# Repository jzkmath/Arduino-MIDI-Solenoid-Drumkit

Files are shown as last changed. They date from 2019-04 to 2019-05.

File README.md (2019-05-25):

# Arduino-MIDI-Solenoid-Drumkit
Uses an Arduino Mega and a custom Shield PCB to drive 14 solenoids (RevA) or 32 solenoids (RevB) via MIDI

## Rev A:
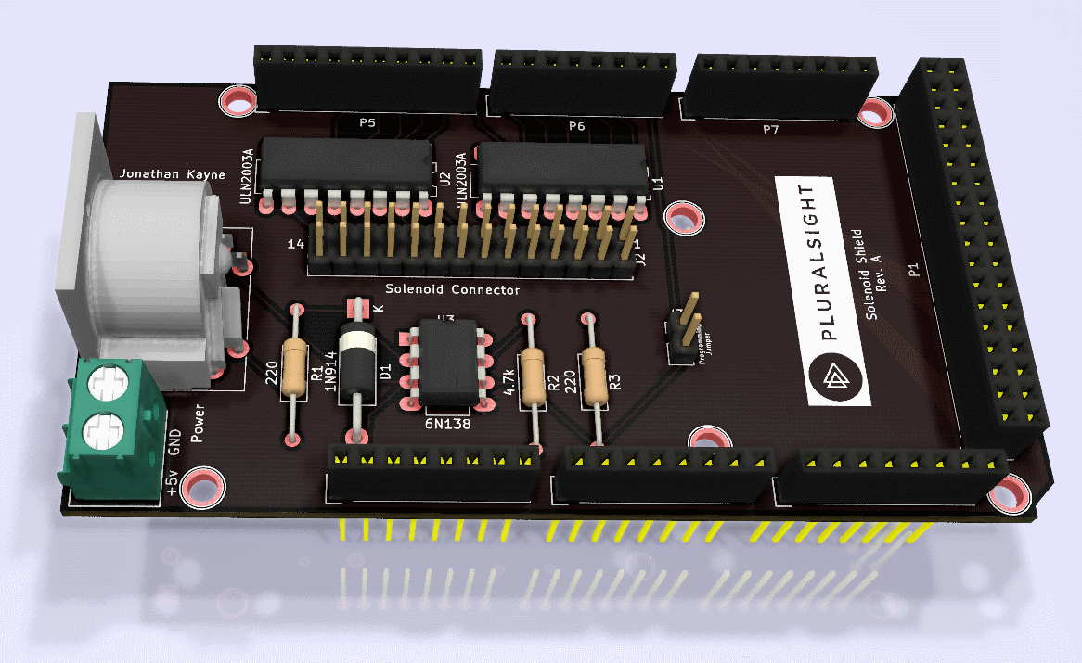
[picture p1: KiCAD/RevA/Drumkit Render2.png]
PCB RevA

## Rev B:
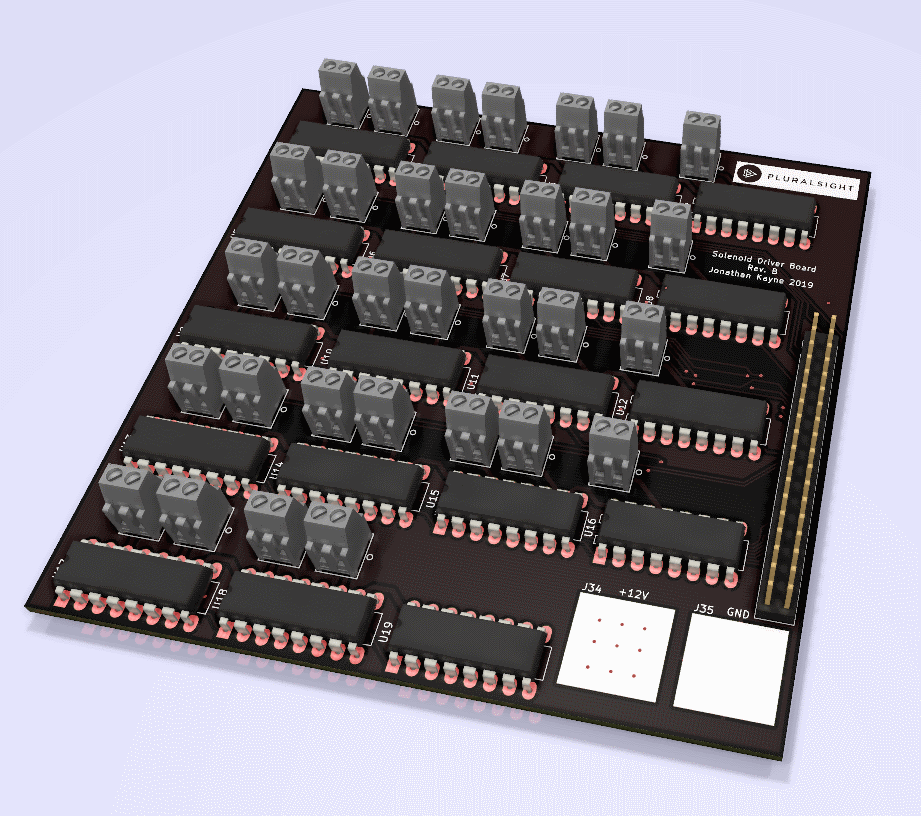
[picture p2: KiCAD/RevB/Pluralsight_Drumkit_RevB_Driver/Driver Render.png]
PCB RevB


This design is based off the [Adafruit Crikit](https://www.adafruit.com/product/3343) and MIDI Solenoid Drumkit that they did, but instead uses a non-blocking delay and can handle more solenoids. The Solenoids are connected to 5V/12V and a Darlington Array (ULN2003A) connects the negative to ground when turned on. 

Just like in the [Adafuit version](https://learn.adafruit.com/midi-solenoid-drummer/overview), the first solenoid corresponds to a C1 (MIDI Note #24) and the following solenoids correspond to the following notes in chromatic order.

## NOTE:
There is a two pin header (J3) that is the programming jumper. The jumper should be installed here and removed when the Arduino is being programmed. This is because the MIDI Rx line is also use to program the Arduino when its being flashed.

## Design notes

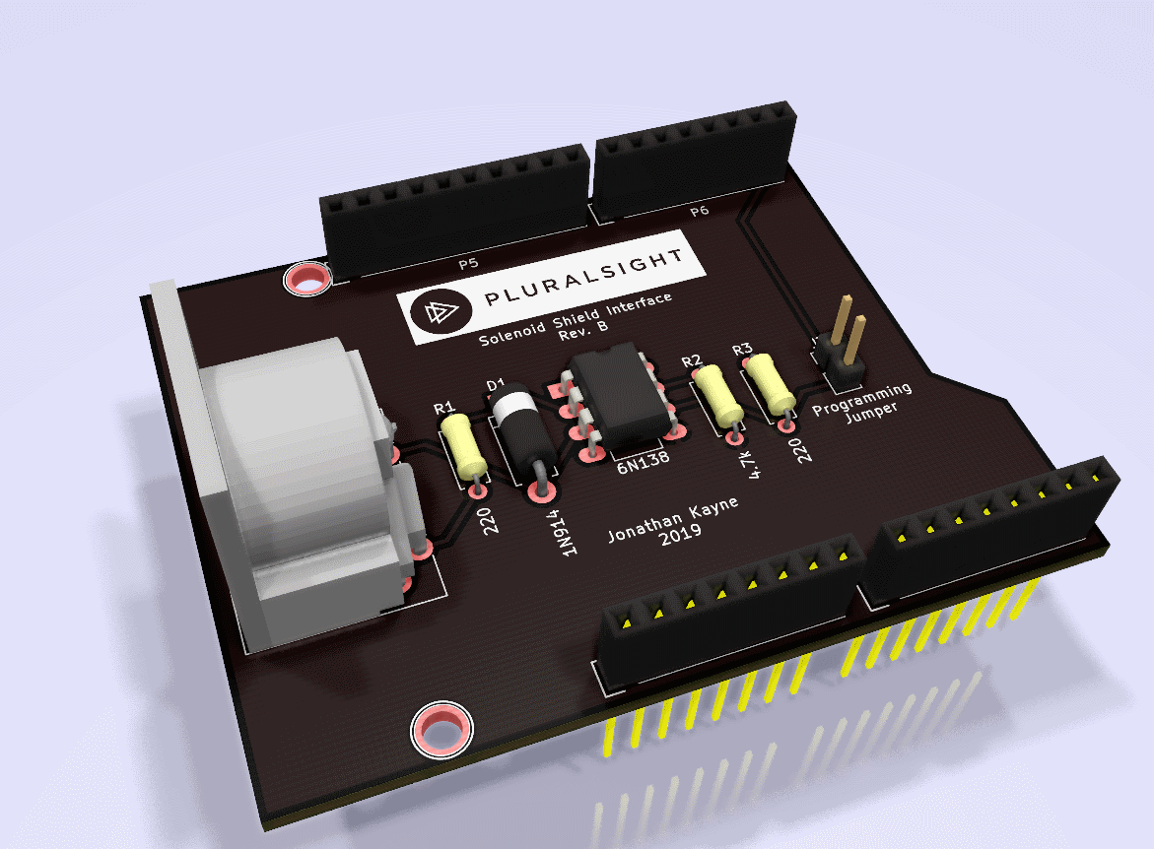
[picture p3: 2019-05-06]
KiCAD/RevB/Pluralsight_Drumkit_RevB_Interface/Interface Render.png

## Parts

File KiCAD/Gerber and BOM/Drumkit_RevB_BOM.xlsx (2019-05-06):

Board | Qty | Reference(s) | Value | Digikey | Cost | Total | Link | Total: | $43.96
Driver | 32 | J1-J33 | 2 pos Screw Terminal | A98333-ND | $0.58 | $18.51 | https://www.digikey.com/short/pzbmff
Both | 2 | J25, P1 | 2x18 Header | 732-5309-ND | $1.72 | $3.44 | https://www.digikey.com/short/pzbh4n
Driver | 2 | J34, J35 | Power | N/A | $0.00 | $0.00 | N/A
Driver | 19 | U1-U19 | ULN2003A | 497-2344-5-ND | $0.59 | $11.21 | https://www.digikey.com/short/pzbmvp
Driver | 19 | U1-U19 | DIP16 Socket | AE9992-ND | $0.24 | $4.48 | https://www.digikey.com/short/pzbm03
Interface | 1 | D1 | 1N914 | 1N914FS-ND | $0.10 | $0.10 | https://www.digikey.com/short/pzbhm2
Interface | 1 | J1 | MIDI DIN Connector | CP-2350-ND | $1.96 | $1.96 | https://www.digikey.com/short/pzbhhp
Interface | 1 | J3 | 1x2 Header | 732-5315-ND | $0.13 | $0.13 | https://www.digikey.com/short/pzbhhw
Interface | 5 | P2-P7 | 1x8 Header | 732-5321-ND | $0.37 | $1.85 | https://www.digikey.com/short/pzbh9m
Interface | 1 | P5 | 1x10 Header | 732-2670-ND | $0.89 | $0.89 | https://www.digikey.com/short/pzbh9v
Interface | 2 | R1, R3 | 220 ohm | S220QCT-ND | $0.10 | $0.20 | https://www.digikey.com/short/pzbhb3
Interface | 1 | R2 | 4.7k | S4.7KQCT-ND | $0.10 | $0.10 | https://www.digikey.com/short/pzbhbw
Interface | 1 | U3 | 6N138 | 160-1795-ND | $0.81 | $0.81 | https://www.digikey.com/short/pzbhrn
Interface | 1 | U3 | DIP8 Socket | AE9986-ND | $0.18 | $0.18 | https://www.digikey.com/short/pzbhft
Interface | 1 | J3 | Jumper | S9337-ND | $0.10 | $0.10 | https://www.digikey.com/short/pzbhf5

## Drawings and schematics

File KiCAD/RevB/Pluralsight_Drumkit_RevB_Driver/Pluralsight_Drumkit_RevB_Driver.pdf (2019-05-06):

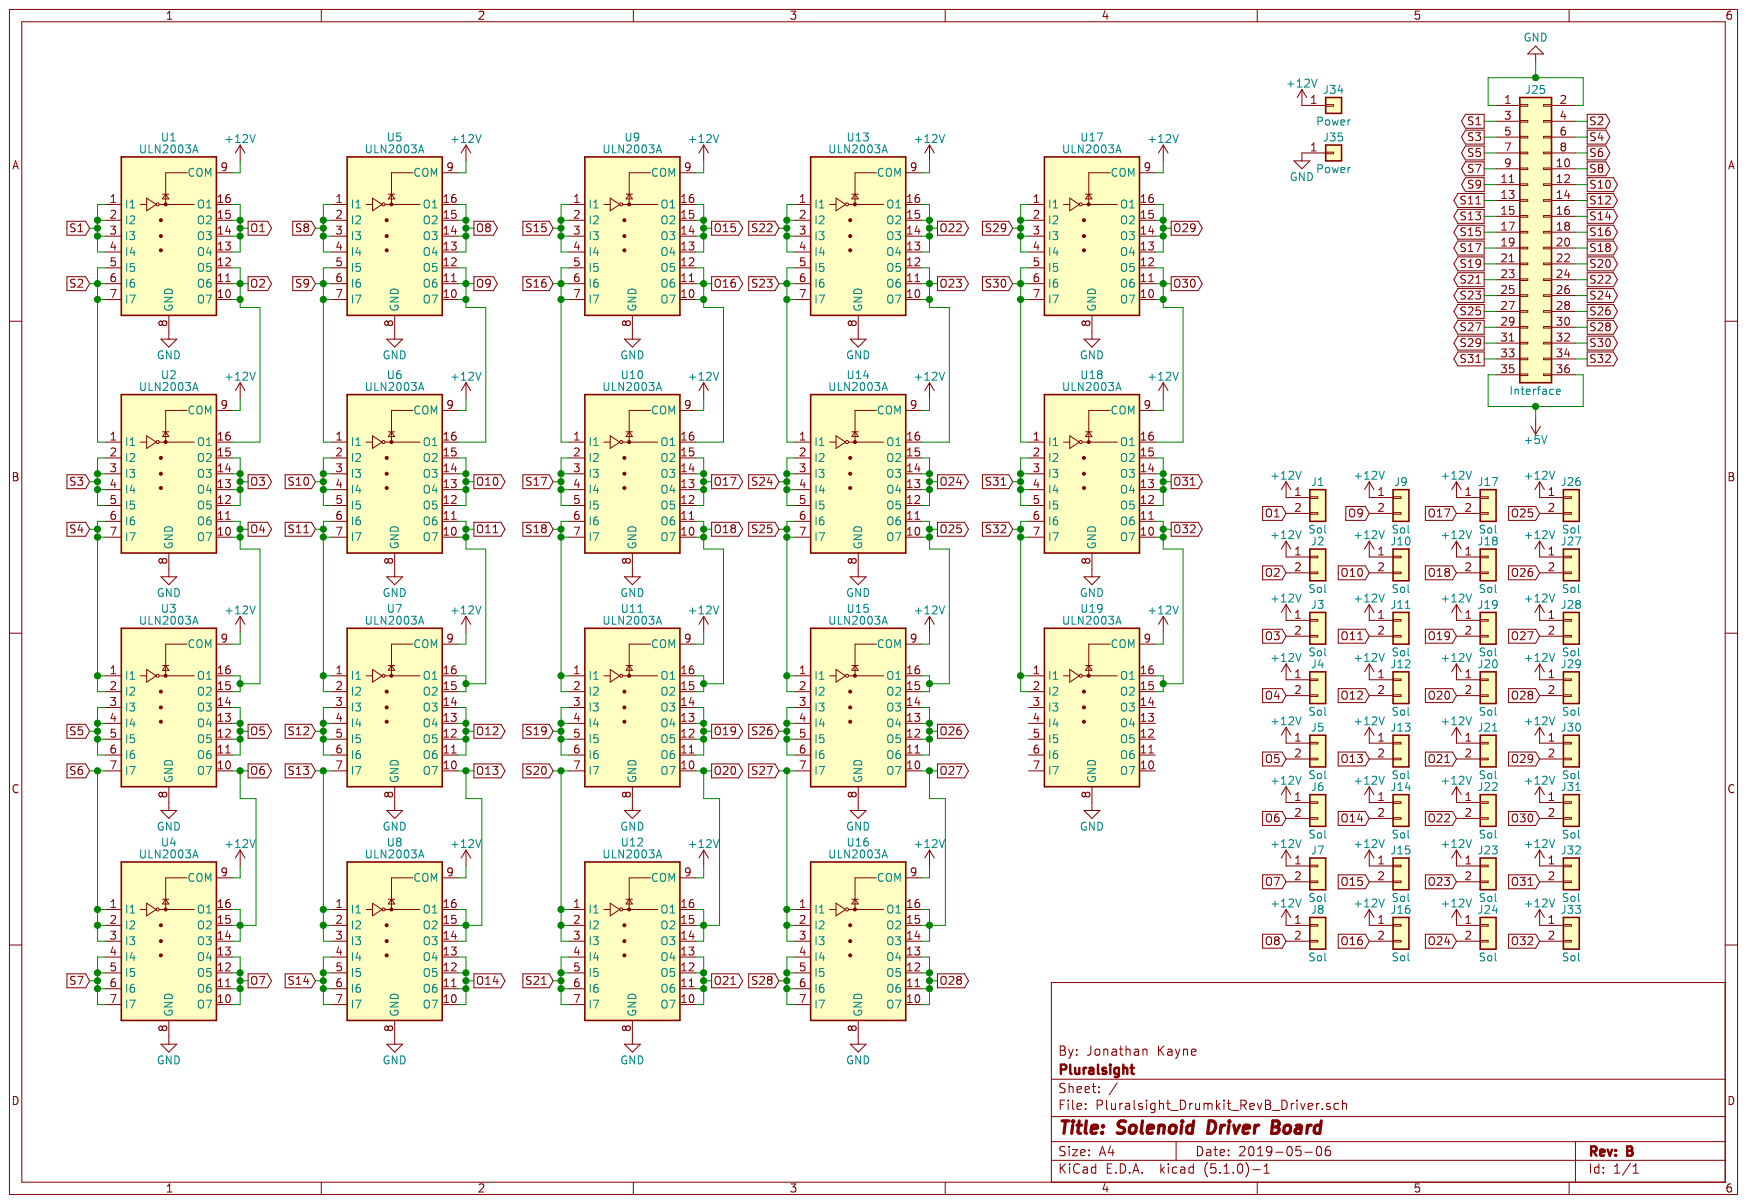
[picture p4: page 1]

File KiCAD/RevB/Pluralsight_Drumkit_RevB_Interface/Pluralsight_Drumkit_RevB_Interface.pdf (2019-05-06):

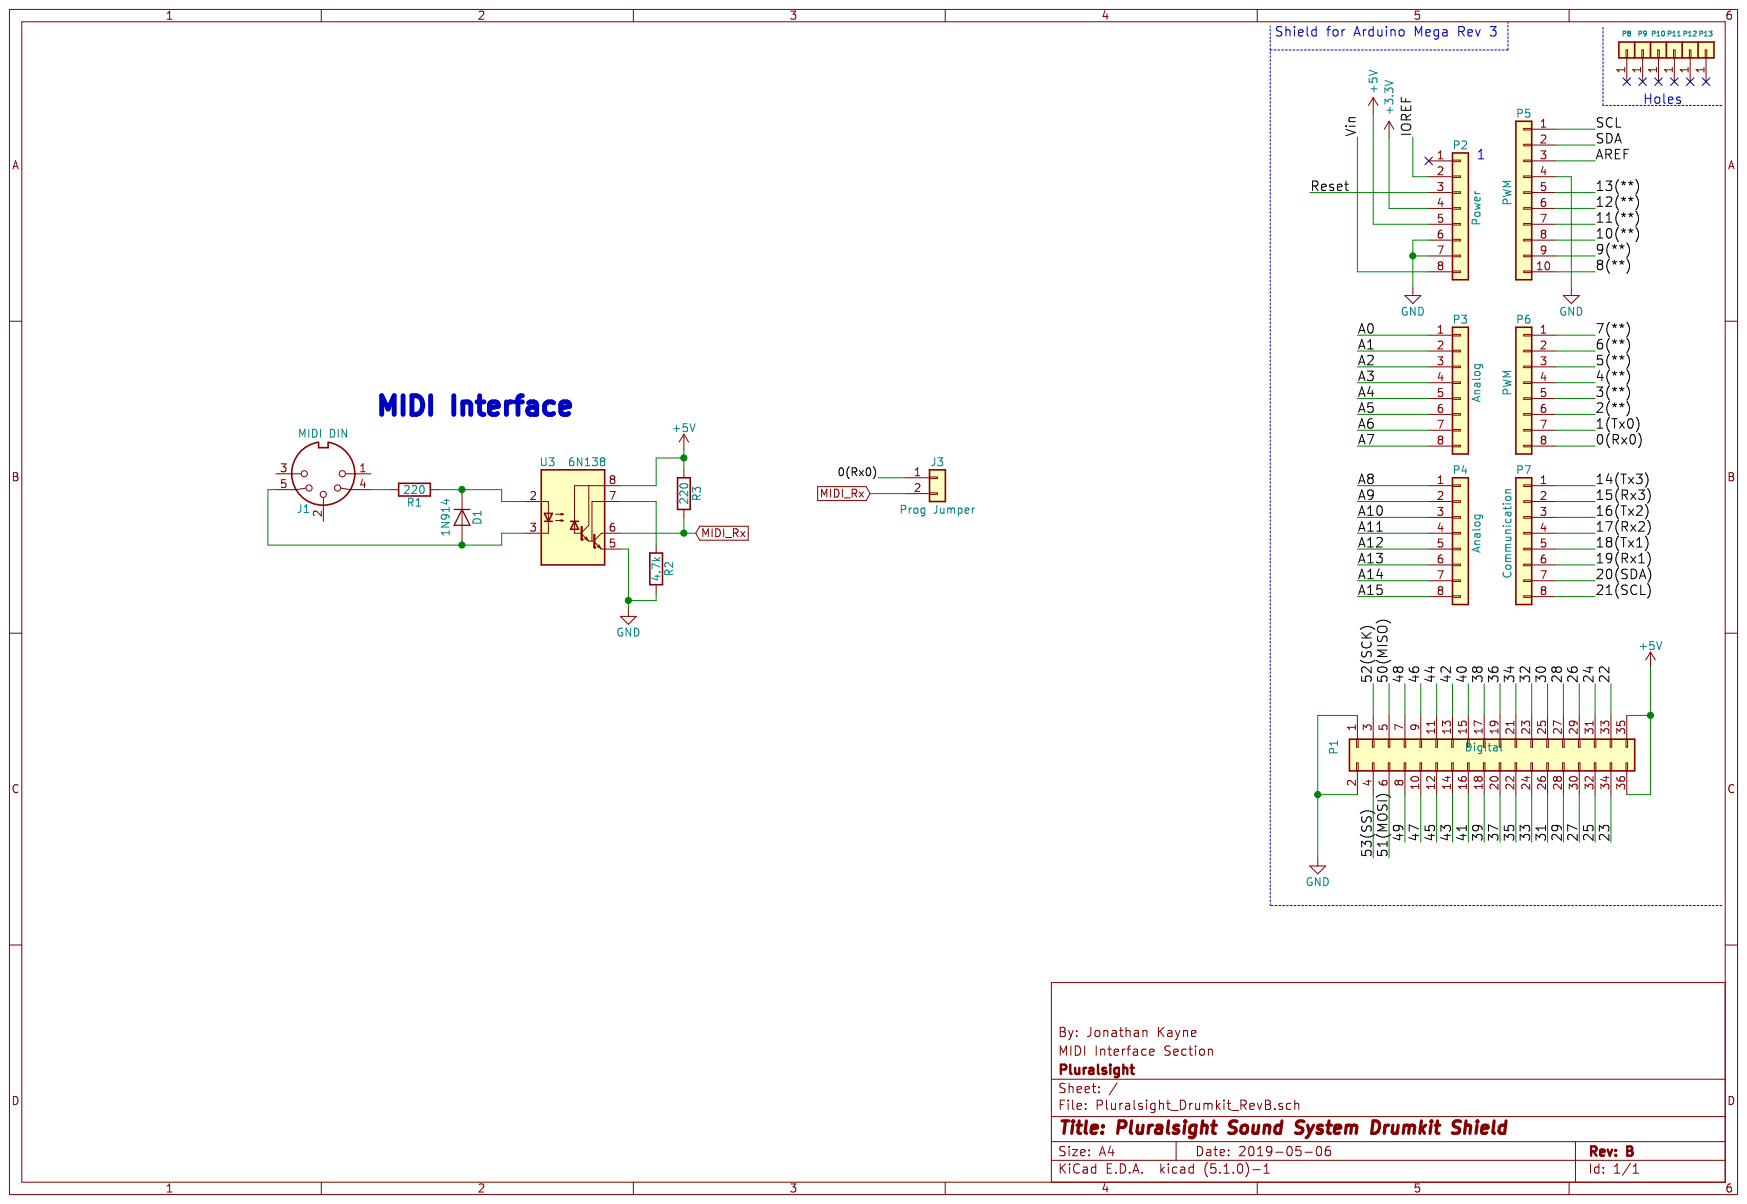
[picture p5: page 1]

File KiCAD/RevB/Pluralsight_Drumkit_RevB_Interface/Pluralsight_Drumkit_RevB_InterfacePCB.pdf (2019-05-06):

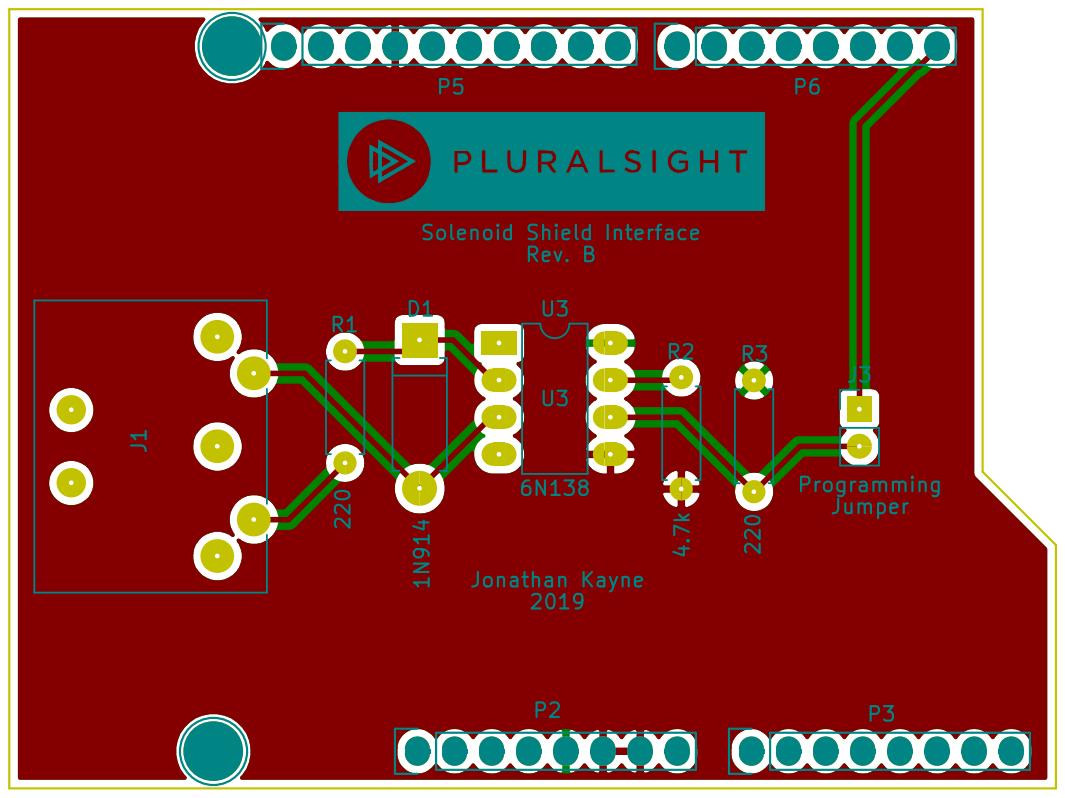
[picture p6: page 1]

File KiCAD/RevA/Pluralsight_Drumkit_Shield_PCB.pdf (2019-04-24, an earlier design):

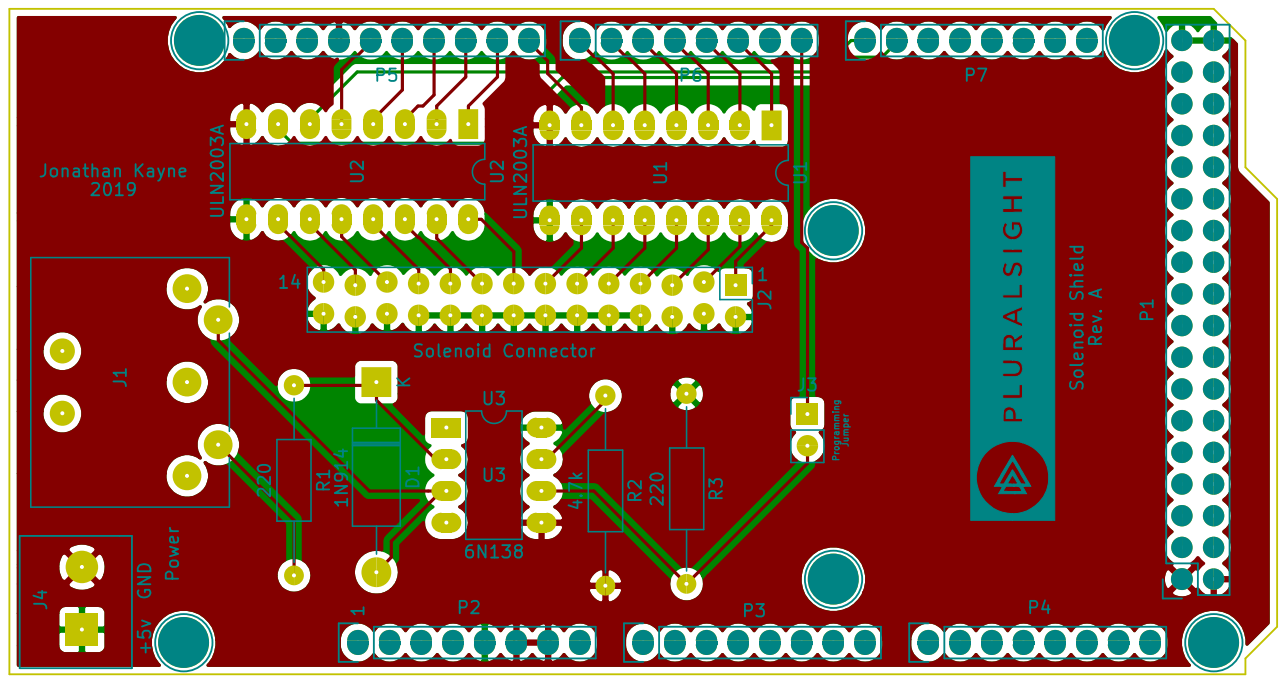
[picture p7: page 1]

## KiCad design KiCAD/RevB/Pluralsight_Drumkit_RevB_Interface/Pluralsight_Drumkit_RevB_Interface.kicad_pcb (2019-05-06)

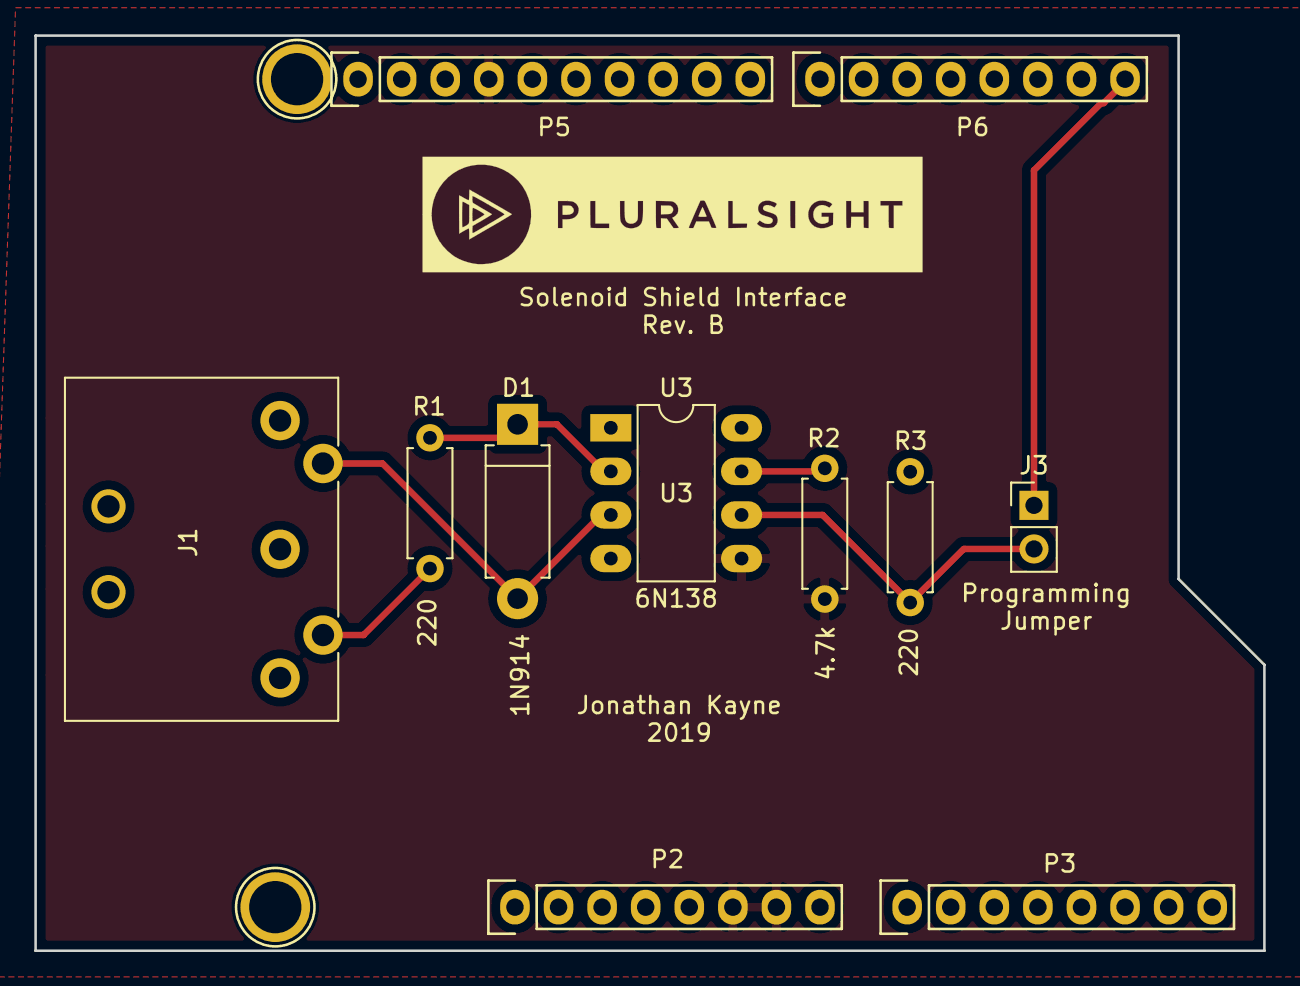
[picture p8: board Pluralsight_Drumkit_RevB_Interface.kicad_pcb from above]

Board: 2 copper layers, 71.6 x 53.3 mm, 13 parts (0 on the bottom side), 8 nets.

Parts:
D1: 1N914; D_DO-15_P10.16mm_Horizontal
J1: MIDI DIN; SDS-50J
J3: Prog Jumper; PinHeader_1x02_P2.54mm_Vertical
P2: Power; Socket_Strip_Arduino_1x08
P3: Analog; Socket_Strip_Arduino_1x08
P5: PWM; Socket_Strip_Arduino_1x10
P6: PWM; Socket_Strip_Arduino_1x08
P8, P11: CONN_01X01; Arduino_1pin
R1, R3: 220; R_Axial_DIN0207_L6.3mm_D2.5mm_P7.62mm_Horizontal
R2: 4.7k; R_Axial_DIN0207_L6.3mm_D2.5mm_P7.62mm_Horizontal
U3: 6N138; DIP-8_W7.62mm_LongPads

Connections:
+5V: P2.5, R3.1, U3.8
/0(Rx0): J3.1, P6.8
GND: P2.6, P2.7, P5.4, R2.2, U3.5
MIDI_Rx: J3.2, R3.2, U3.6
unnamed: D1.1, R1.1, U3.2
unnamed: D1.2, J1.5, U3.3
unnamed: J1.4, R1.2
unnamed: R2.1, U3.7

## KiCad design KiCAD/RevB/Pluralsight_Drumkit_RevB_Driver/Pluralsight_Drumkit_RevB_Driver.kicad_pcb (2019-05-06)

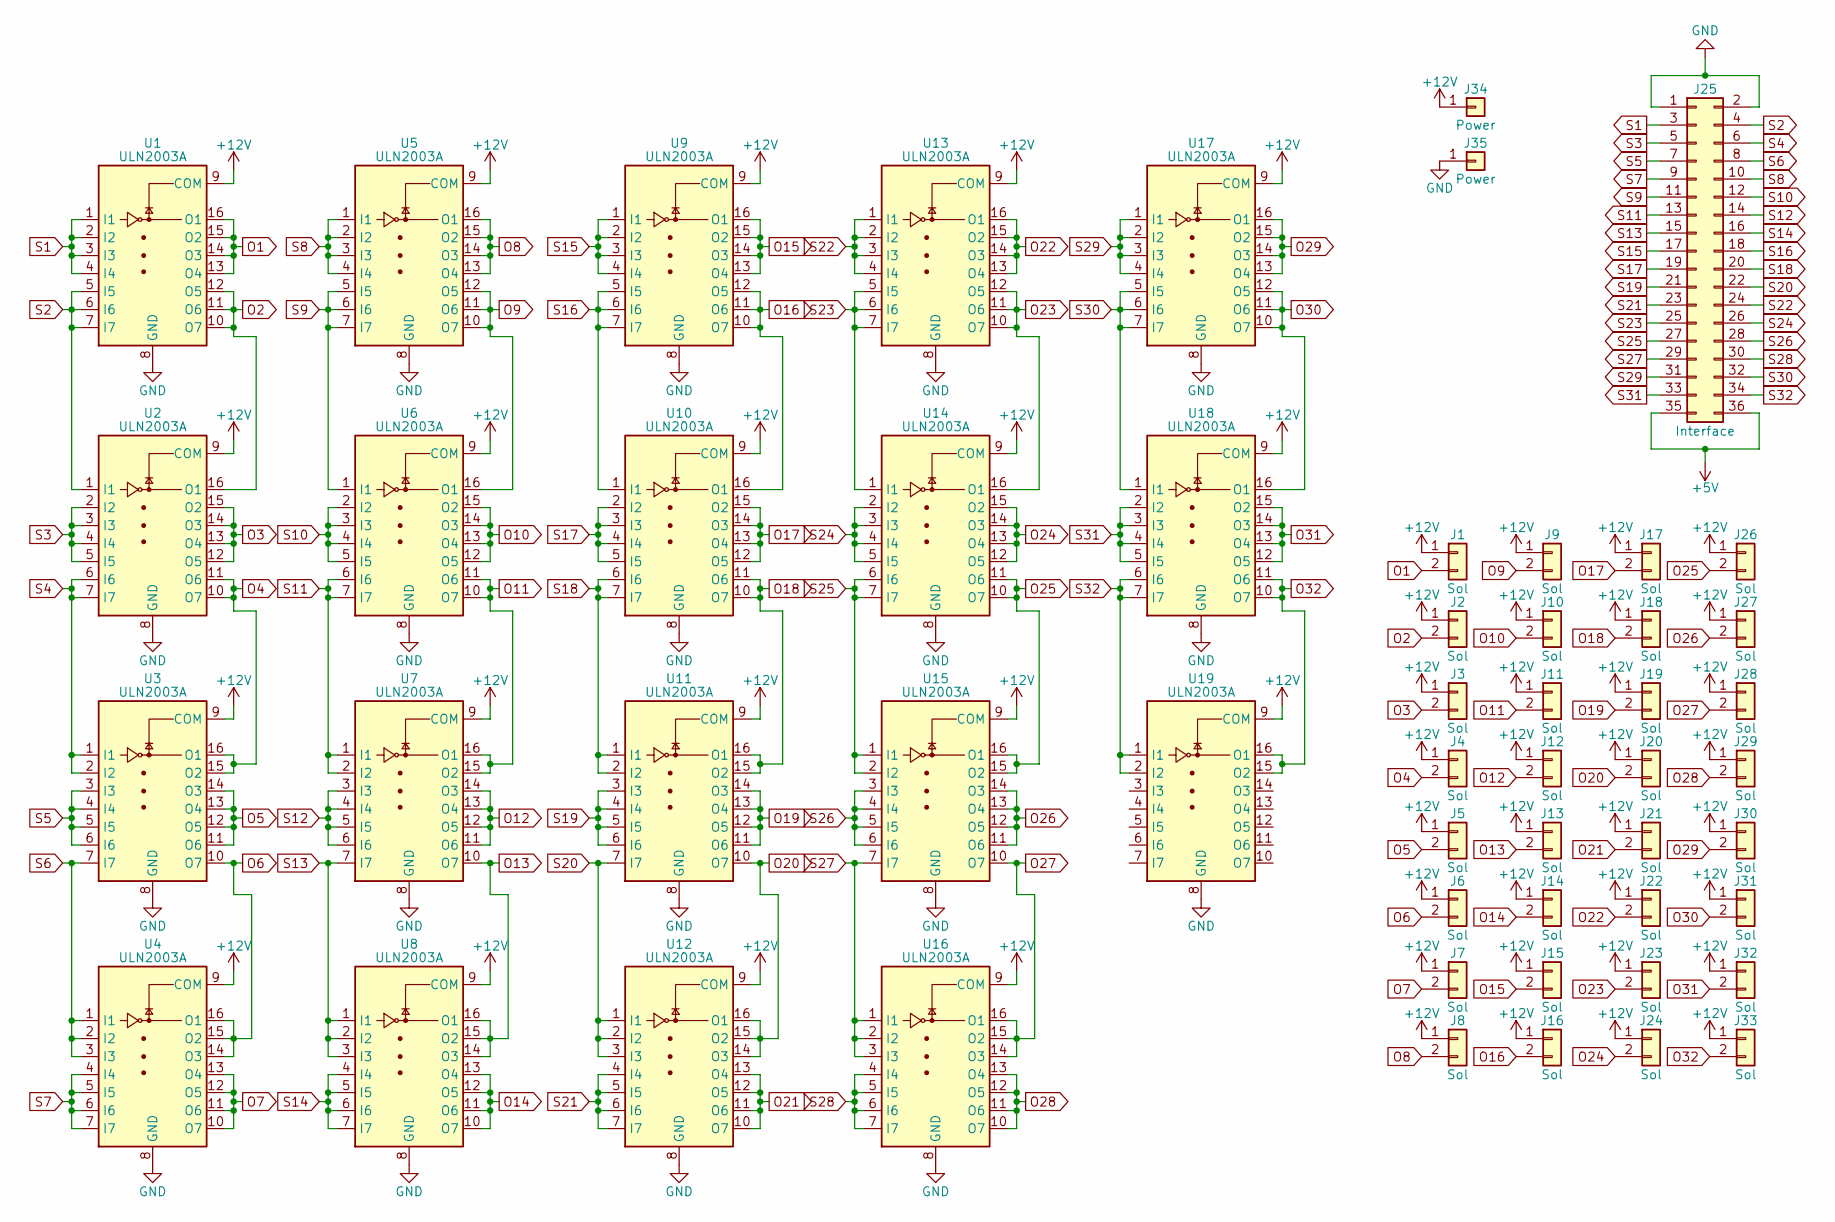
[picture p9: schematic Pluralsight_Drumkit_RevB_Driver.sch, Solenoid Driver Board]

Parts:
J1, J2, J3, J4, J5, J6, J7, J8, J9, J10, J11, J12, J13, J14, J15, J16, J17, J18, J19, J20, J21, J22, J23, J24, J26, J27, J28, J29, J30, J31, J32, J33: Sol; ScrewTerm_282834-2
J25: Interface; PinHeader_2x18_P2.54mm_Vertical
J34, J35: Power; SolderPadPower
U1, U2, U3, U4, U5, U6, U7, U8, U9, U10, U11, U12, U13, U14, U15, U16, U17, U18, U19: ULN2003A; DIP-16_W7.62mm_LongPads

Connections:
+12V: J1.1, J2.1, J3.1, J4.1, J5.1, J6.1, J7.1, J8.1, J9.1, J10.1, J11.1, J12.1, J13.1, J14.1, J15.1, J16.1, J17.1, J18.1, J19.1, J20.1, J21.1, J22.1, J23.1, J24.1, J26.1, J27.1, J28.1, J29.1, J30.1, J31.1, J32.1, J33.1, J34.1, U1.9 (COM), U2.9 (COM), U3.9 (COM), U4.9 (COM), U5.9 (COM), U6.9 (COM), U7.9 (COM), U8.9 (COM), U9.9 (COM), U10.9 (COM), U11.9 (COM), U12.9 (COM), U13.9 (COM), U14.9 (COM), U15.9 (COM), U16.9 (COM), U17.9 (COM), U18.9 (COM), U19.9 (COM)
GND: J25.1, J25.2, J35.1, U1.8 (GND), U2.8 (GND), U3.8 (GND), U4.8 (GND), U5.8 (GND), U6.8 (GND), U7.8 (GND), U8.8 (GND), U9.8 (GND), U10.8 (GND), U11.8 (GND), U12.8 (GND), U13.8 (GND), U14.8 (GND), U15.8 (GND), U16.8 (GND), U17.8 (GND), U18.8 (GND), U19.8 (GND)
O1: J1.2, U1.13 (O4), U1.14 (O3), U1.15 (O2), U1.16 (O1)
O2: J2.2, U1.10 (O7), U1.11 (O6), U1.12 (O5), U2.16 (O1)
O3: J3.2, U2.12 (O5), U2.13 (O4), U2.14 (O3), U2.15 (O2)
O4: J4.2, U2.10 (O7), U2.11 (O6), U3.15 (O2), U3.16 (O1)
O5: J5.2, U3.11 (O6), U3.12 (O5), U3.13 (O4), U3.14 (O3)
O6: J6.2, U3.10 (O7), U4.14 (O3), U4.15 (O2), U4.16 (O1)
O7: J7.2, U4.10 (O7), U4.11 (O6), U4.12 (O5), U4.13 (O4)
O8: J8.2, U5.13 (O4), U5.14 (O3), U5.15 (O2), U5.16 (O1)
O9: J9.2, U5.10 (O7), U5.11 (O6), U5.12 (O5), U6.16 (O1)
O10: J10.2, U6.12 (O5), U6.13 (O4), U6.14 (O3), U6.15 (O2)
O11: J11.2, U6.10 (O7), U6.11 (O6), U7.15 (O2), U7.16 (O1)
O12: J12.2, U7.11 (O6), U7.12 (O5), U7.13 (O4), U7.14 (O3)
O13: J13.2, U7.10 (O7), U8.14 (O3), U8.15 (O2), U8.16 (O1)
O14: J14.2, U8.10 (O7), U8.11 (O6), U8.12 (O5), U8.13 (O4)
O15: J15.2, U9.13 (O4), U9.14 (O3), U9.15 (O2), U9.16 (O1)
O16: J16.2, U9.10 (O7), U9.11 (O6), U9.12 (O5), U10.16 (O1)
O17: J17.2, U10.12 (O5), U10.13 (O4), U10.14 (O3), U10.15 (O2)
O18: J18.2, U10.10 (O7), U10.11 (O6), U11.15 (O2), U11.16 (O1)
O19: J19.2, U11.11 (O6), U11.12 (O5), U11.13 (O4), U11.14 (O3)
O20: J20.2, U11.10 (O7), U12.14 (O3), U12.15 (O2), U12.16 (O1)
O21: J21.2, U12.10 (O7), U12.11 (O6), U12.12 (O5), U12.13 (O4)
O22: J22.2, U13.13 (O4), U13.14 (O3), U13.15 (O2), U13.16 (O1)
O23: J23.2, U13.10 (O7), U13.11 (O6), U13.12 (O5), U14.16 (O1)
O24: J24.2, U14.12 (O5), U14.13 (O4), U14.14 (O3), U14.15 (O2)
O25: J26.2, U14.10 (O7), U14.11 (O6), U15.15 (O2), U15.16 (O1)
O26: J27.2, U15.11 (O6), U15.12 (O5), U15.13 (O4), U15.14 (O3)
O27: J28.2, U15.10 (O7), U16.14 (O3), U16.15 (O2), U16.16 (O1)
O28: J29.2, U16.10 (O7), U16.11 (O6), U16.12 (O5), U16.13 (O4)
O29: J30.2, U17.13 (O4), U17.14 (O3), U17.15 (O2), U17.16 (O1)
O30: J31.2, U17.10 (O7), U17.11 (O6), U17.12 (O5), U18.16 (O1)
O31: J32.2, U18.12 (O5), U18.13 (O4), U18.14 (O3), U18.15 (O2)
O32: J33.2, U18.10 (O7), U18.11 (O6), U19.15 (O2), U19.16 (O1)
S1: J25.3, U1.1 (I1), U1.2 (I2), U1.3 (I3), U1.4 (I4)
S2: J25.4, U1.5 (I5), U1.6 (I6), U1.7 (I7), U2.1 (I1)
S3: J25.5, U2.2 (I2), U2.3 (I3), U2.4 (I4), U2.5 (I5)
S4: J25.6, U2.6 (I6), U2.7 (I7), U3.1 (I1), U3.2 (I2)
S5: J25.7, U3.3 (I3), U3.4 (I4), U3.5 (I5), U3.6 (I6)
S6: J25.8, U3.7 (I7), U4.1 (I1), U4.2 (I2), U4.3 (I3)
S7: J25.9, U4.4 (I4), U4.5 (I5), U4.6 (I6), U4.7 (I7)
S8: J25.10, U5.1 (I1), U5.2 (I2), U5.3 (I3), U5.4 (I4)
S9: J25.11, U5.5 (I5), U5.6 (I6), U5.7 (I7), U6.1 (I1)
S10: J25.12, U6.2 (I2), U6.3 (I3), U6.4 (I4), U6.5 (I5)
S11: J25.13, U6.6 (I6), U6.7 (I7), U7.1 (I1), U7.2 (I2)
S12: J25.14, U7.3 (I3), U7.4 (I4), U7.5 (I5), U7.6 (I6)
S13: J25.15, U7.7 (I7), U8.1 (I1), U8.2 (I2), U8.3 (I3)
S14: J25.16, U8.4 (I4), U8.5 (I5), U8.6 (I6), U8.7 (I7)
S15: J25.17, U9.1 (I1), U9.2 (I2), U9.3 (I3), U9.4 (I4)
S16: J25.18, U9.5 (I5), U9.6 (I6), U9.7 (I7), U10.1 (I1)
S17: J25.19, U10.2 (I2), U10.3 (I3), U10.4 (I4), U10.5 (I5)
S18: J25.20, U10.6 (I6), U10.7 (I7), U11.1 (I1), U11.2 (I2)
S19: J25.21, U11.3 (I3), U11.4 (I4), U11.5 (I5), U11.6 (I6)
S20: J25.22, U11.7 (I7), U12.1 (I1), U12.2 (I2), U12.3 (I3)
S21: J25.23, U12.4 (I4), U12.5 (I5), U12.6 (I6), U12.7 (I7)
S22: J25.24, U13.1 (I1), U13.2 (I2), U13.3 (I3), U13.4 (I4)
S23: J25.25, U13.5 (I5), U13.6 (I6), U13.7 (I7), U14.1 (I1)
S24: J25.26, U14.2 (I2), U14.3 (I3), U14.4 (I4), U14.5 (I5)
S25: J25.27, U14.6 (I6), U14.7 (I7), U15.1 (I1), U15.2 (I2)
S26: J25.28, U15.3 (I3), U15.4 (I4), U15.5 (I5), U15.6 (I6)
S27: J25.29, U15.7 (I7), U16.1 (I1), U16.2 (I2), U16.3 (I3)
S28: J25.30, U16.4 (I4), U16.5 (I5), U16.6 (I6), U16.7 (I7)
S29: J25.31, U17.1 (I1), U17.2 (I2), U17.3 (I3), U17.4 (I4)
S30: J25.32, U17.5 (I5), U17.6 (I6), U17.7 (I7), U18.1 (I1)
S31: J25.33, U18.2 (I2), U18.3 (I3), U18.4 (I4), U18.5 (I5)
S32: J25.34, U18.6 (I6), U18.7 (I7), U19.1 (I1), U19.2 (I2)

Board: 2 copper layers, 54 parts (0 on the bottom side), 66 nets, no tracks yet.

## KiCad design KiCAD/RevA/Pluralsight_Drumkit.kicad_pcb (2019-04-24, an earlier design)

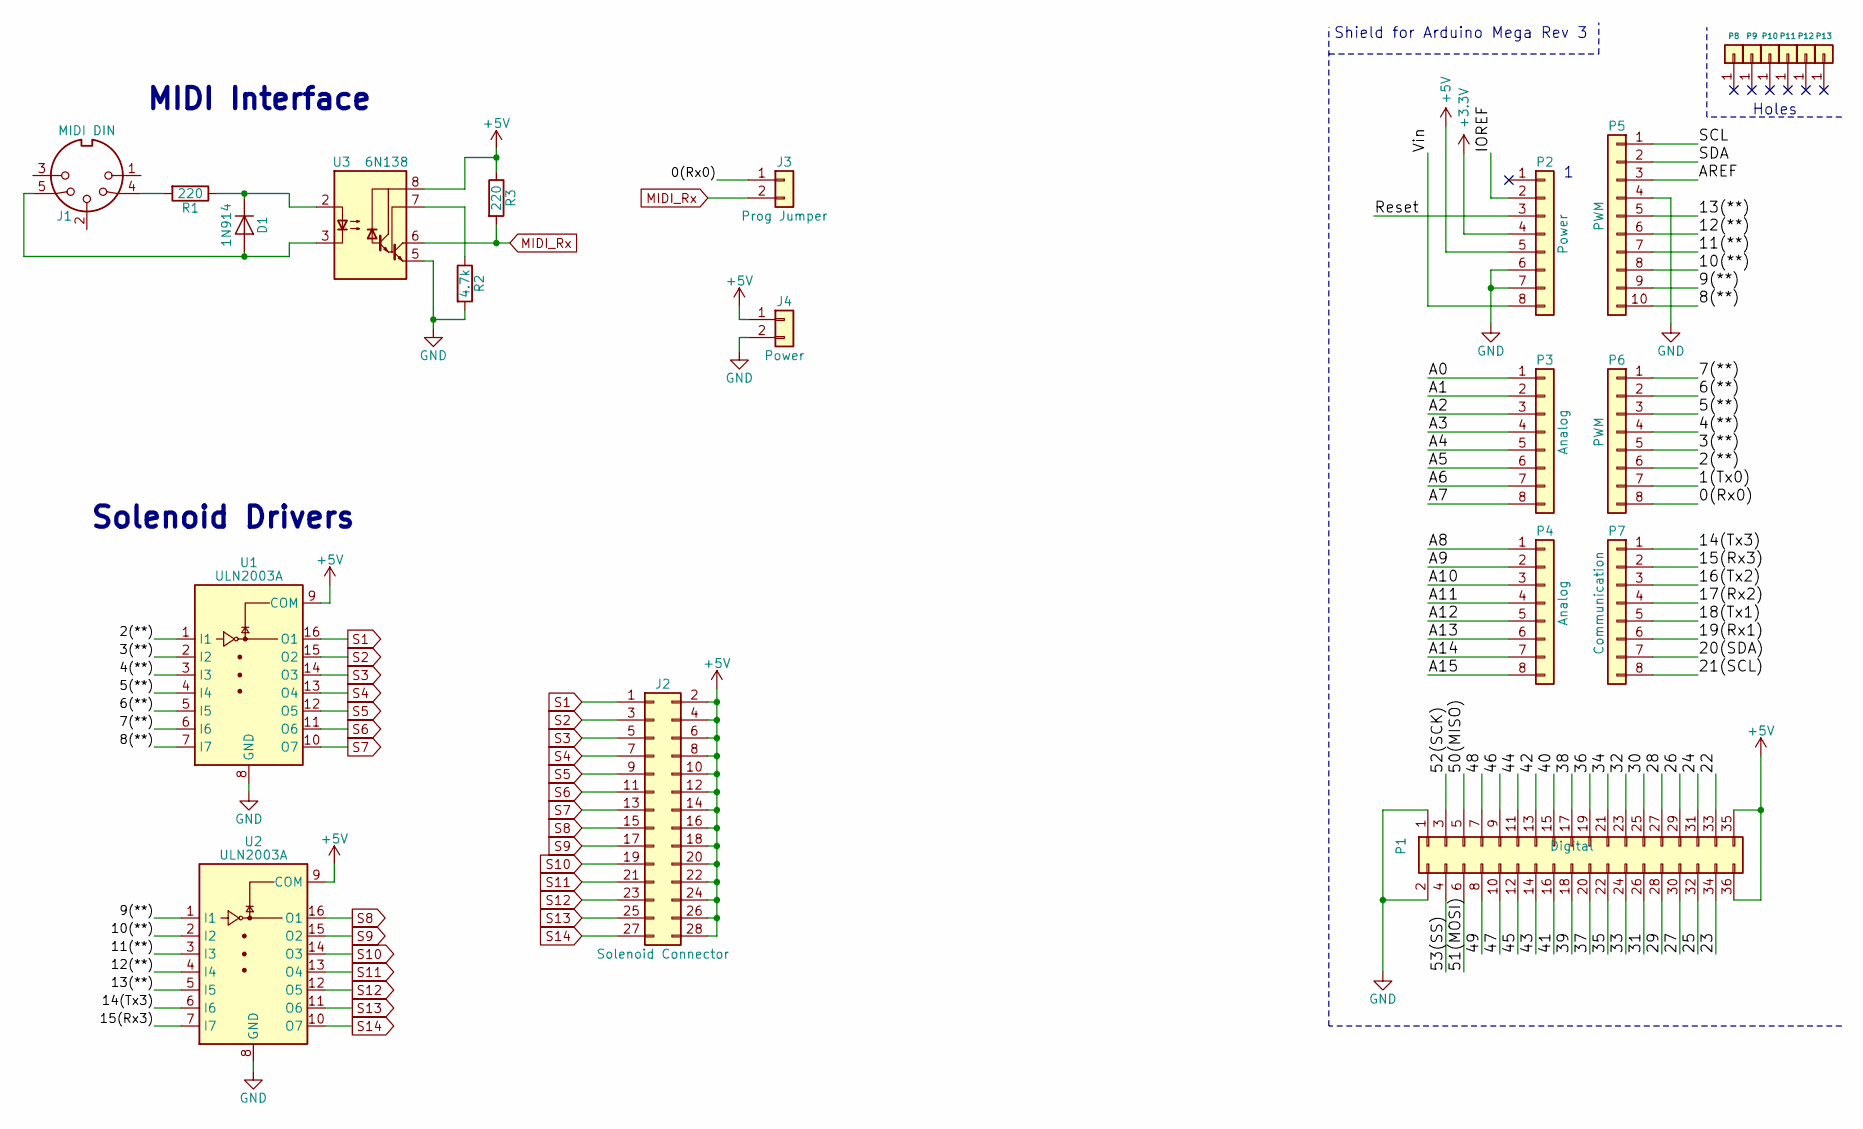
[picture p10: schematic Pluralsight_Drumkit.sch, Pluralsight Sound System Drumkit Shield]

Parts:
D1: 1N914; D_DO-15_P15.24mm_Horizontal
J1: MIDI DIN; SDS-50J
J2: Solenoid Connector; PinHeader_2x14_P2.54mm_Vertical_zigzag
J3: Prog Jumper; PinHeader_1x02_P2.54mm_Vertical
J4: Power; 2_Pos_Screw_Term
P1: Digital; Socket_Strip_Arduino_2x18
P2: Power; Socket_Strip_Arduino_1x08
P3, P4: Analog; Socket_Strip_Arduino_1x08
P5: PWM; Socket_Strip_Arduino_1x10
P6: PWM; Socket_Strip_Arduino_1x08
P7: Communication; Socket_Strip_Arduino_1x08
P8, P9, P10, P11, P12, P13: CONN_01X01; Arduino_1pin
R1, R3: 220; R_Axial_DIN0207_L6.3mm_D2.5mm_P15.24mm_Horizontal
R2: 4.7k; R_Axial_DIN0207_L6.3mm_D2.5mm_P15.24mm_Horizontal
U1, U2: ULN2003A; DIP-16_W7.62mm_LongPads
U3: 6N138; DIP-8_W7.62mm_LongPads

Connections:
+3V3: P2.4
+5V: J2.2, J2.4, J2.6, J2.8, J2.10, J2.12, J2.14, J2.16, J2.18, J2.20, J2.22, J2.24, J2.26, J2.28, J4.1, P1.35, P1.36, P2.5, R3.1, U1.9 (COM), U2.9 (COM), U3.8 (VCC)
/0(Rx0): J3.1, P6.8
/1(Tx0): P6.7
/2(**): P6.6, U1.1 (I1)
/3(**): P6.5, U1.2 (I2)
/4(**): P6.4, U1.3 (I3)
/5(**): P6.3, U1.4 (I4)
/6(**): P6.2, U1.5 (I5)
/7(**): P6.1, U1.6 (I6)
/8(**): P5.10, U1.7 (I7)
/9(**): P5.9, U2.1 (I1)
/10(**): P5.8, U2.2 (I2)
/11(**): P5.7, U2.3 (I3)
/12(**): P5.6, U2.4 (I4)
/13(**): P5.5, U2.5 (I5)
/14(Tx3): P7.1, U2.6 (I6)
/15(Rx3): P7.2, U2.7 (I7)
/16(Tx2): P7.3
/17(Rx2): P7.4
/18(Tx1): P7.5
/19(Rx1): P7.6
/20(SDA): P7.7
/21(SCL): P7.8
/22: P1.33
/23: P1.34
/24: P1.31
/25: P1.32
/26: P1.29
/27: P1.30
/28: P1.27
/29: P1.28
/30: P1.25
/31: P1.26
/32: P1.23
/33: P1.24
/34: P1.21
/35: P1.22
/36: P1.19
/37: P1.20
/38: P1.17
/39: P1.18
/40: P1.15
/41: P1.16
/42: P1.13
/43: P1.14
/44: P1.11
/45: P1.12
/46: P1.9
/47: P1.10
/48: P1.7
/49: P1.8
/50(MISO): P1.5
/51(MOSI): P1.6
/52(SCK): P1.3
/53(SS): P1.4
/A0: P3.1
/A1: P3.2
/A2: P3.3
/A3: P3.4
/A4: P3.5
/A5: P3.6
/A6: P3.7
/A7: P3.8
/A8: P4.1
/A9: P4.2
/A10: P4.3
/A11: P4.4
/A12: P4.5
/A13: P4.6
/A14: P4.7
/A15: P4.8
/AREF: P5.3
/IOREF: P2.2
/Reset: P2.3
/SCL: P5.1
/SDA: P5.2
/Vin: P2.8
GND: J4.2, P1.1, P1.2, P2.6, P2.7, P5.4, R2.2, U1.8 (GND), U2.8 (GND), U3.5 (GND)
MIDI_Rx: J3.2, R3.2, U3.6 (VO2)
unnamed: D1.1 (K), R1.1, U3.2 (C1)
unnamed: D1.2 (A), J1.5, U3.3 (C2)
unnamed: J1.4, R1.2
unnamed: R2.1, U3.7 (VO1)
S1: J2.1, U1.16 (O1)
S2: J2.3, U1.15 (O2)
S3: J2.5, U1.14 (O3)
S4: J2.7, U1.13 (O4)
S5: J2.9, U1.12 (O5)
S6: J2.11, U1.11 (O6)
S7: J2.13, U1.10 (O7)
S8: J2.15, U2.16 (O1)
S9: J2.17, U2.15 (O2)
S10: J2.19, U2.14 (O3)
S11: J2.21, U2.13 (O4)
S12: J2.23, U2.12 (O5)
S13: J2.25, U2.11 (O6)
S14: J2.27, U2.10 (O7)

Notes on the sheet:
Shield for Arduino Mega Rev 3
Holes
MIDI Interface
Solenoid Drivers

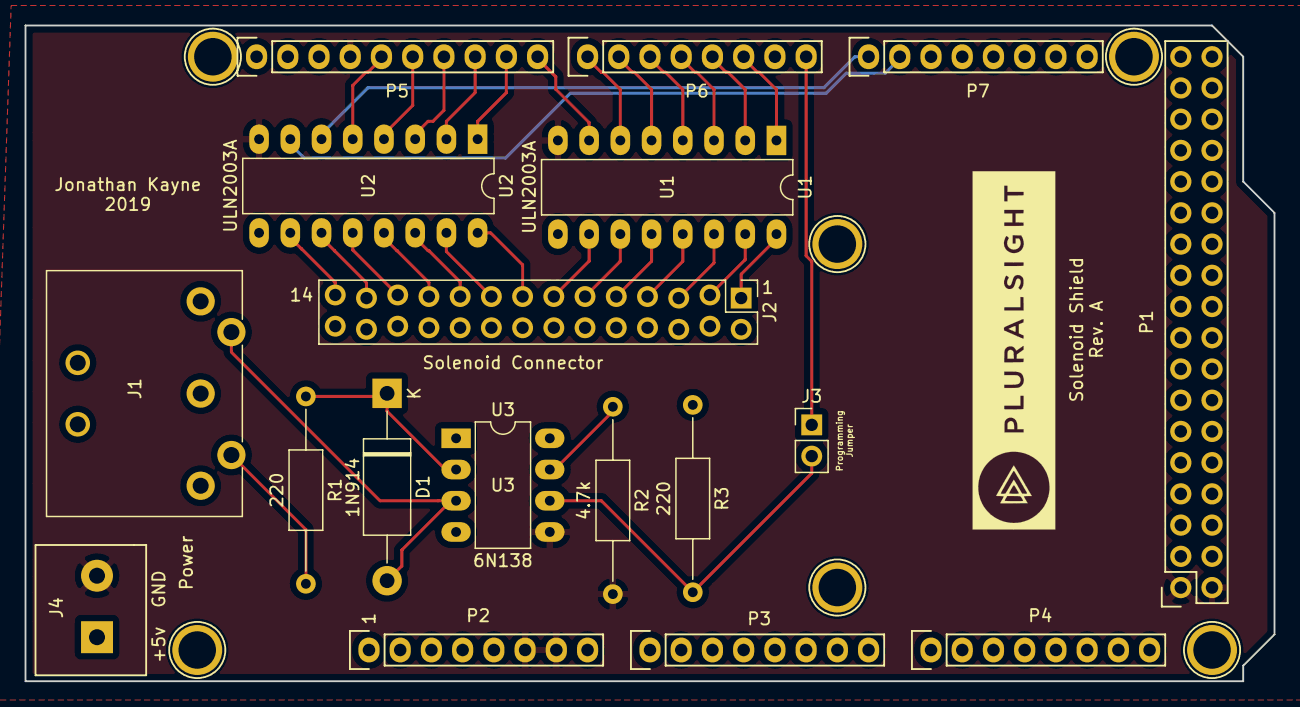
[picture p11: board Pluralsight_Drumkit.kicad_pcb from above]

Board: 2 copper layers, 101.6 x 53.3 mm, 24 parts (0 on the bottom side), 36 nets.

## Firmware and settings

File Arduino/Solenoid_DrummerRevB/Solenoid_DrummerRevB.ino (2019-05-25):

#include <MIDI.h>

/*
 * ARDUINO MIDI SOLENOID DRUMKIT
 * By: Jonathan Kayne, 2019
 * 
 * This program uses an Arduino Mega with a custom Shield
 * to drive 32 solenoids as drums.
 * This is based off the Adafruit version, but does not
 * have the same limitations due the use of a non-blocking delay.
 */

 #define NUM_SOLENOIDS 32

 //The delay value in milliseconds for the on time
 #define HIT_DURATION 8

 //variables
 unsigned const solenoidPins[] = {53, 52, 51, 50, 49, 48, 47, 46, 45, 44, 43, 42, 41, 40, 39, 38, 37, 36, 35, 34, 33, 32, 31, 30, 29, 28, 27, 26, 25, 24, 23, 22};
 unsigned long prevOnTimeMillis[] = {0, 0, 0, 0, 0, 0, 0, 0, 0, 0, 0, 0, 0, 0, 0, 0, 0, 0, 0, 0, 0, 0, 0, 0, 0, 0, 0, 0, 0, 0, 0, 0}; //holds the last time the motor was turned on
 bool solenoidState[] = {LOW, LOW, LOW, LOW, LOW, LOW, LOW, LOW, LOW, LOW, LOW, LOW, LOW, LOW, LOW, LOW, LOW, LOW, LOW, LOW, LOW, LOW, LOW, LOW, LOW, LOW, LOW, LOW, LOW, LOW, LOW, LOW}; //keep track of the solenoid state

 MIDI_CREATE_DEFAULT_INSTANCE(); //use default MIDI settings
 

void setup() {
  //set solenoids as outputs
  for (int s = 0; s < NUM_SOLENOIDS; s++)
  {
    pinMode(solenoidPins[s], OUTPUT);
    digitalWrite(solenoidPins[2], LOW);
  }
 
  MIDI.begin(MIDI_CHANNEL_OMNI); //listen to all MIDI channels
  MIDI.setHandleNoteOn(handleNoteOn); //execute function when note on message is recieved
}

void loop() 
{
  MIDI.read(); //read MIDI messages
  turnOffSolenoid();  //reset solenoid after a certain duration
}

void handleNoteOn(byte channel, byte pitch, byte velocity) //MIDI Note ON Command
{
  int solenoid = pitch - 24; //which solenoid to activate
  // when a C1 is played, the first solenoid will be selected, because 
  // MIDI pitch 24 corresponds to C1.

  digitalWrite(solenoidPins[solenoid], HIGH); //turn on selected solenoid
  solenoidState[solenoid] = HIGH; //set state to true
  prevOnTimeMillis[solenoid] = millis(); //update time
  
}

void turnOffSolenoid()
{
  for (int i = 0; i < NUM_SOLENOIDS; i++)
  {
    //when the time has elapsed and the solenoid is on turn off the solenoid
    if ((millis() - prevOnTimeMillis[i] >= HIT_DURATION) && (solenoidState == 1))
    {
      digitalWrite(solenoidPins[i], LOW);
      solenoidState[i] = LOW;
    }
  }
}

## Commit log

2019-04-24 Added Arduino Code V1
2019-04-24 Added KiCAD files
    [Pluralsight_Drumkit.kicad_pcb, Pluralsight_Drumkit.sch]
2019-04-24 Added Gerber and BOM
    [Drumkit_BOM.xlsx]
2019-04-26 Added Digikey BOM
    [Drumkit_BOM.xlsx, Drumkit_DigikeyBOM.csv, Pluralsight_Drumkit.sch]
2019-05-06 added RevB
    [Drumkit_RevA_BOM.xlsx, Drumkit_RevA_DigikeyBOM.csv, Drumkit_RevB_BOM.xlsx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]
